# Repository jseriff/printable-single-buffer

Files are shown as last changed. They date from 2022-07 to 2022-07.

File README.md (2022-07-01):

# Printable Single Loop Buffer

**Beta Quality - Use at your own risk**

This is a single loop, expandable buffer for use with the Enraged Rabbit Carrot Feeder, or other MMU.  Each buffer assembly deals with one color, you can print as many as you need.  You can print as many extensions as required to buffer any length, although only ~950mm (500mm of extensions) has been tested by me.  It is intended to be mounted to 2020 extensions, but anything should work.

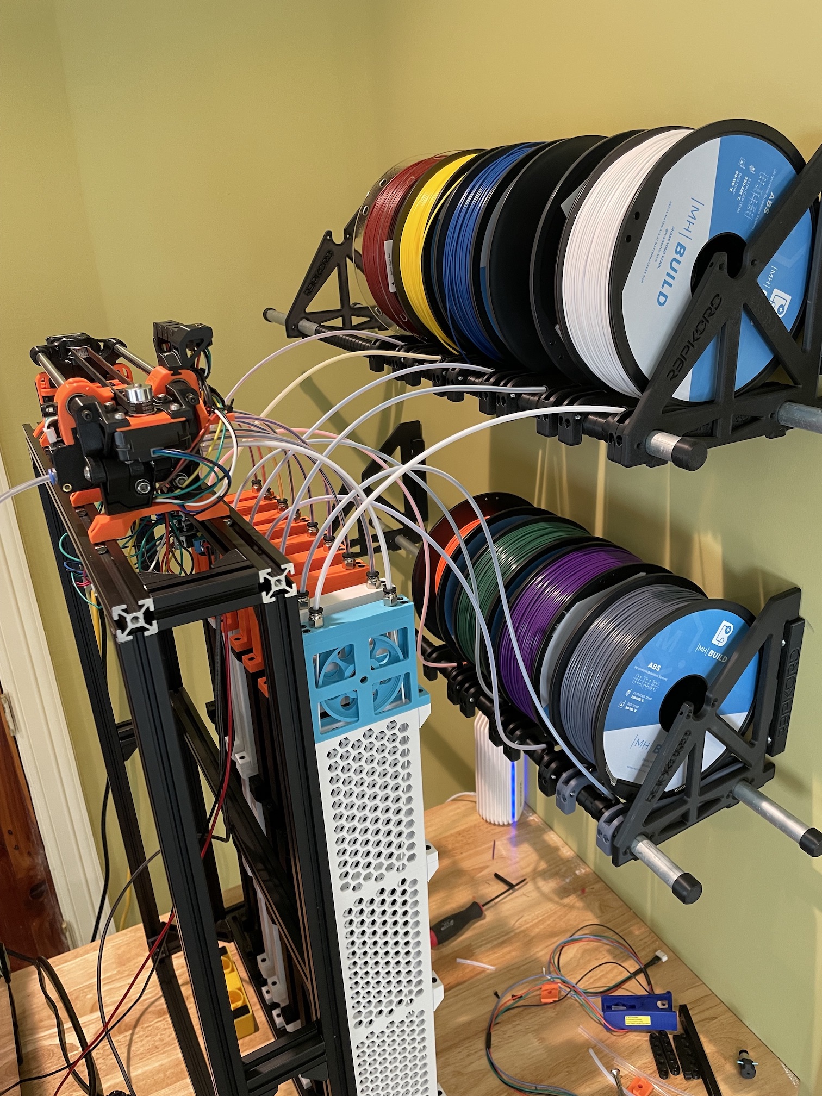
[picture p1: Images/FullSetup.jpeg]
Full Setup


The project is generated with a code CAD tool called CadQuery - STLs and STEP files are generated from that, but the python file is the source of truth.  To get this to work in CadQuery, you must also use the cq_warehouse extension, including a custom connector defined as "13/32-28 asme_b18.3"

### Each Buffer Requires

#### Printable Parts
** Parts may not be properly aligned - use your judgment **
* buffer_intake.stl
* buffer_mount_a.stl
* buffer_mount_b.stl
* buffer_wheel.stl
* Some number of buffer_extensions_<X>.stl - X is the height of the extension in MM, you height needs to total slightly over half your reverse bowden length. You can mix and match these within a single buffer.

#### Other Parts
* 608 Bearing
* 2 PC4-M10 pass through bowden couplers
* 6 M3 Heat set inserts (Voron Standard)
* 2 M3 Heat set inserts per extension
* 6 M3x10 
* 2 M3x10 per extension
* 1 M3x12

### Assembly

* Add heatset inserts to the 4 screw holes on top of the A/B buffer mounts (the holes closest to the edges)
* Add a heatset insert to the flat side of the B mount, in the center
* Insert the bearing into the wheel
* Place the Buffer Mount A and B on either side of the wheel, with the bearing on the center post, and use hte M3x12 to attach.  Dont hulk this, you dont want to bind the wheel
* Screw the Intake to the top with M3x10
* Insert the Bowden couplers into the intake
* For each extension:  Add 2x heatset inserts to the top mounting holes - the orientation of the extension is the angled mounts are top, squared are bottom.
* To attach, use M3x10 from the buffer mount to the first extension, and so on
* Insert bowden tubes and push through until they hit plastic

### Notes

* There is also an STL for a mounting connector.  You can place this between two extensions (using longer screws), and use the additional screw holes to mount this to an extrusion or something else for stability.  I have my buffers mounted to extrusions only on the bottom, and they are surprisngly rigid and did not require this additional side mount.
* I use 3mm ID tube from the filament to the buffer, and 2.5mm ID for a small jump from the buffer to the ERCF
* The stl files are all tested, but the STEP file is not

### TODO

- [ ] Change mounting block on the buffer mount A/B so the screw captures both parts and the B mount is not "hanging loose"
- [ ] Add cutouts to the sides of the extensions to reduce plastic usage and provide better visibility
- [ ] Add small chamfer to inside of PTFE holes in buffer mount, to make loading/unloading a little easier
- [ ] Widen the entire assembly to make loading/unloading easier and reduce some friction on the filament
- [ ] Change the buffer mount attachment to no longer require removing screws to change filament

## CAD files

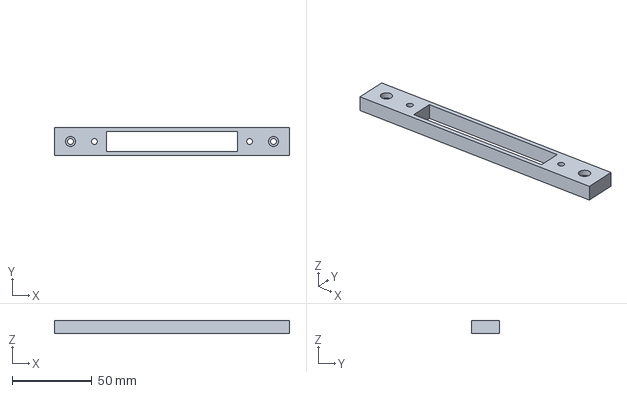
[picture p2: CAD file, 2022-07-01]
CAD/buffer_extrusion_mount.step
147.0 x 17.8 x 8.00 mm

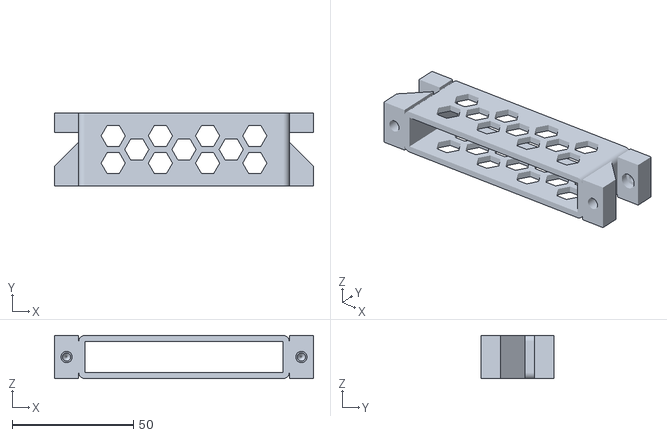
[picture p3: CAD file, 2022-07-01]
STLs/buffer_extension_30.stl
107.0 x 30.0 x 17.8

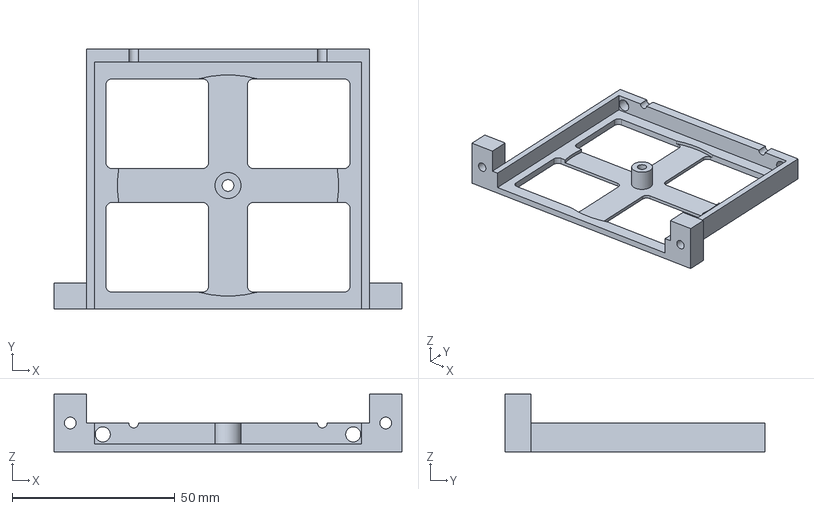
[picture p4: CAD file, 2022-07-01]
CAD/buffer_mount_a.step
107.0 x 80.0 x 17.8 mm

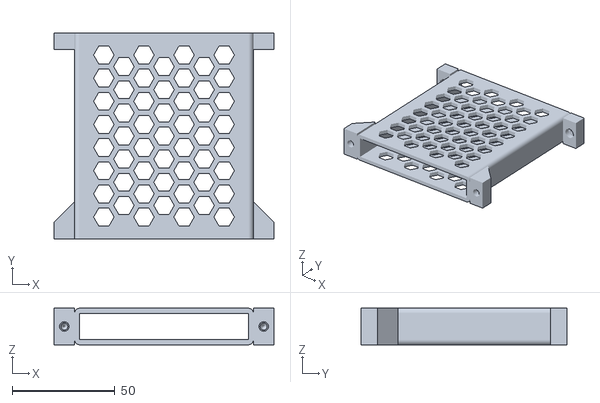
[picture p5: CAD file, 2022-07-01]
STLs/buffer_extension_100.stl
107.0 x 100.0 x 17.8

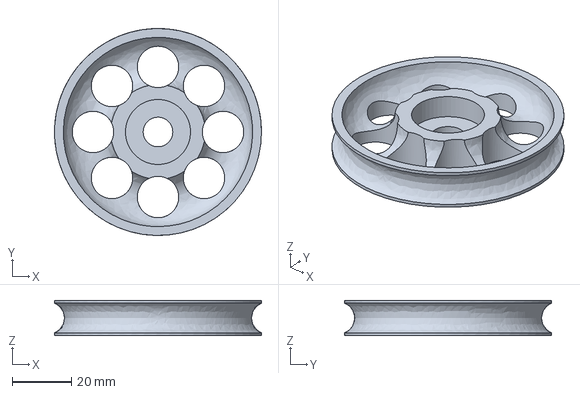
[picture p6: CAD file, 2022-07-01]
CAD/buffer_wheel.step
70.0 x 70.0 x 12.0 mm

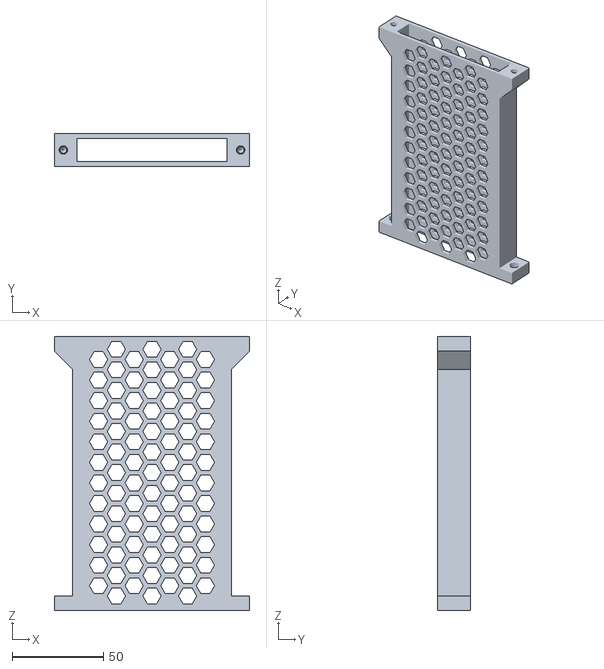
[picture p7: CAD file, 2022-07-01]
STLs/buffer_extension_150.stl
107.0 x 17.8 x 150.0

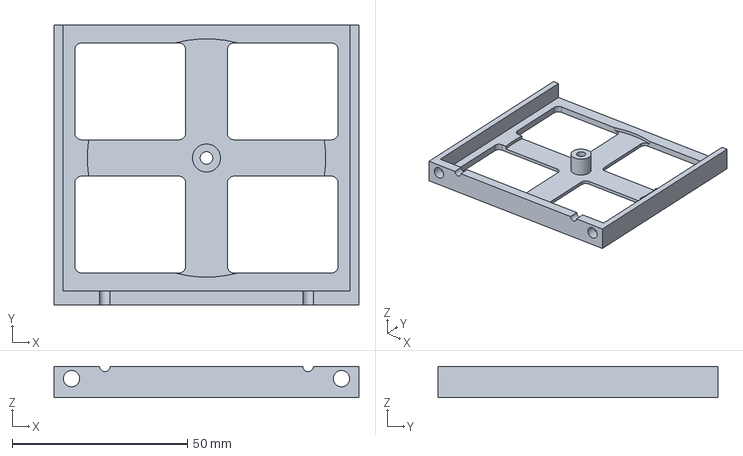
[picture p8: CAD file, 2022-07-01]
CAD/buffer_mount_b.step
87.0 x 80.0 x 8.90 mm

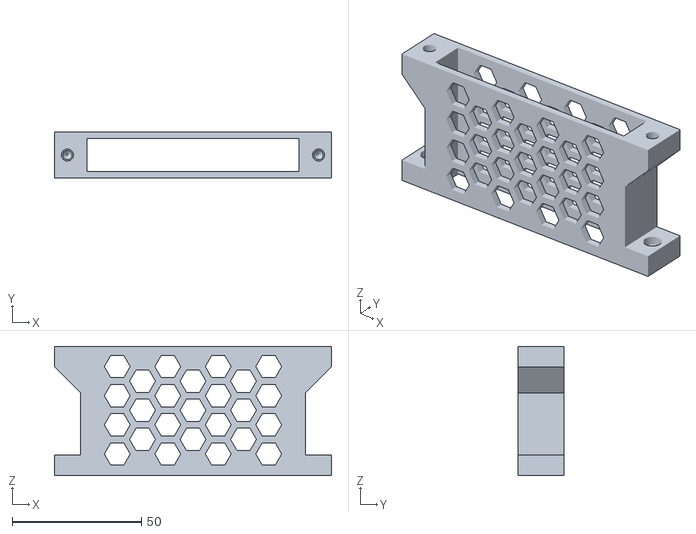
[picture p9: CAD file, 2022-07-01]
STLs/buffer_extension_50.stl
107.0 x 17.8 x 50.0

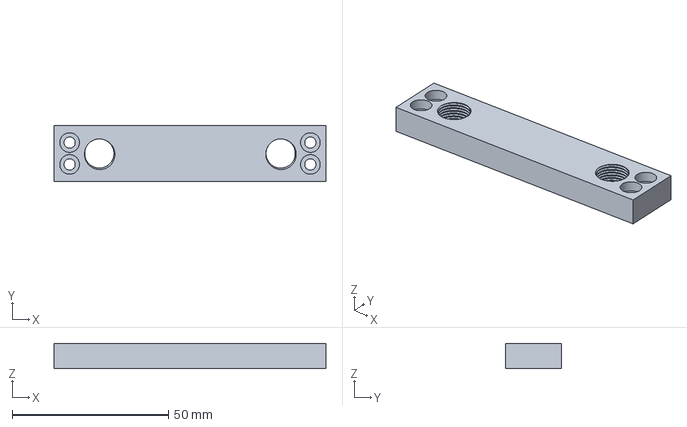
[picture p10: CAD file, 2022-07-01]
CAD/buffer_intake.step
87.0 x 17.8 x 8.00 mm

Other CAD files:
STLs/buffer_extrusion_mount.stl
STLs/buffer_intake.stl
STLs/buffer_mount_a.stl
STLs/buffer_mount_b.stl

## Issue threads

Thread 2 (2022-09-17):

Some Enhancements

whi-tw, 2022-09-17:
Hello!

So, I've been looking for a good buffer solution, and this one works really well!

I have made some changes. Unfortunately CadQuery won't work properly on my machine (M1 Mac), so I have had to use the tools I am used to (onshape). Unfortunately this has meant I've had to re-design a number of parts, as 'deriving' from STEP files is a bit garbage.

The onshape document is here: [Printable Single Buffer - Onshape](https://cad.onshape.com/documents/c077698dfc872e829578f5ba/w/f31ef546889f82207067c550/e/840d972e22b2d8906e45ddef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).

Key changes:
* add some extra geometry to the shaft the bearing sits on, to ensure the bearing sits in the right place, not too close to either of the covers
* Increase the size of the hole on the 'back' of the wheel, to stop it from rubbing against the center of the bearing
* Allow an ECAS bowden inlet to be used, rather than a screw-in one (I have a large number of these left over from my ERCF build).
* Create an extra part to allow the 'wheelhouse' to be magnetically attached to the rest of the buffer, rather than screwed in.
    * This makes threading new filament in, and allows the wheel to be more enclosed
* Increase the diameter of the cutouts in the wheelhouse, to increase clearance to avoid rubbing.
* Improve alignment of filament inlet, so the filament goes in a straight line directly to the edge of the wheel

I've also redone all the extensions, so they all match. The 150mm one seems different to all the others, and seems to be 'right'.

This means the BOM needs:

* 4x M3x8 SHCS
* 2n M3x8 SHCS (n=number of buffer extensions)
* 1x M3x12 (potentially should be longer)
* 1x 608ZZ
* 4x 3x6mm magnets (same as the ones in the ERCF BOM)
* 2x ECAS bowden inlet

I haven't yet had a chance to investigate mounting, but that's my next job.
